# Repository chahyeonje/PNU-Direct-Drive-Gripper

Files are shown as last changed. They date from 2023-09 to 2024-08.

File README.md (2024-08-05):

# Overview

-----

# Table of Contents

- [Preparation](#preparation)
  - [Bill of Materials (BOM)](#bom)
    - [Off-the-Shelf Parts](#purchase)
    - [3D Printing](#3d-printing)
- [Actuators](#actuators)
  - [Actuator Assembly ⨉4](#assemble-actuators)
  - [Wiring](#wiring)
    - [Power Supply](#power-supply)
    - [Encoder Connection](#encoder-connection)
    - [Motor Connection](#Motor-connection)
  - [Actuator Calibration](#actuator-calibration)
    - [Calibrate ODrives](#calibrate-odrives)
    - [Calibrate Zero Position](#calibrate-zero-position)
- [Gripper](#Gripper)
  - [Finger Assembly ⨉2](#finger)
  - [Gripper Assembly](#gripper-assembly)
  - [Mounting](#mounting-ur10)
  - [Validation](#validation)
- [Customization](#customization)
  - [Mounting](#custom-mounting)
  - [Geometry](#geometry)
  - [Fingertip](#fingertip)
- [Getting Started](#getting-started)
  
-----

# Hardeware

## Bill of materials(BOM)

### Off-the-shelf parts
- [T-motor gb54-2](https://store.tmotor.com/goods-445-GB54-2.html) X 4
- [Odrive s1](https://odriverobotics.com/shop/odrive-s1) X 4
- [AS5048A Encoder + solid magnet](https://ko.aliexpress.com/item/1005004239532357.html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) X 4
- [Bearing - outer-diameter = 100mm, inner-diamter = 6mm](https://kr.misumi-ec.com/vona2/detail/221000058378/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) X 12
- [Dowel pin - diameter = 6mm, length = 10mm](https://ko.aliexpress.com/item/1005003326358562.html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) X 6
- [Wire terminal box](https://mini.freeship.co.kr/goods/content.asp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) X 1
- Shielded cable
- 3-phase cable

### 3D Printing
- [Adapter plate](stl/adapter_plate.stl/) X 4
- [Bearing spacer](stl/bearing_spacer.STL) X 12
- [Calibration arm](stl/calibration_arm.STL) X 1
- [Calibration stand](stl/calibration_stand.STL) X 1
- [Coupler](stl/coupler.STL) X 1
- [Couping](stl/coupling.stl) X 1
- [Distal link](stl/distal_link.STL) X 2
- [Distal tip link](stl/distal_tip_link.STL) X 2
- [Finger tip](stl/finger_tip.STL) X 2
- [Gripper shell](stl/gripper_shell.stl) X 1
- [Magnet holder](stl/magnet_holder.STL) X 4
- [Motor plate](stl/motor_plate.stl) X 4
- [Proximal link](stl/proximal_link.STL) X 4
<br/><br/>The gripper is designed to be compatible with Rainbow robotics RB5. For other robot systems, it should be better to design your own adapter plate and coupling.

# Actuators
## Acutator assembly
motor_with_magnet
motor-plate
actuator-module

## Wiring
The components should be connected following the diagram below. The encoder connection(black) and power connection(green) will be further elaborated.
 wiring

### Power Supply
First connect the DC power supply to the wall plug. Then connect it to the four ODrive boards, positive to positive, negetaive to negative. There is no on/off button on the boards, plug in the wall plug to turn the system on, unplug to turn it off.
power_supply

### Encoder Connection
For the encoder connection, we fabricate a cable assembly as shown below in the schematic. It is recommended to verify the connectivity and resistance of each connection to make sure the cables are soldered properly. We also recommend to label each connector like the schematic.

encoder_wiring
encoder_odrive

After successful fabrication, connect the motor encoders and the ODrives.

### Motor Connection
Keep the 3-phase connection consistent as shown below.
wiring-power
motor_odrive

### Odirve S1 Pin map.



# Actuator Calibration

Each actuator module require calibration before use. This step __can not__ be done after the gripper is assembled, so do not postpone this step.

We explicitly define the `direction of the rotor` to be the direction the hexagonal logo on the rotor is pointing at, and the `zero position of the motor` to be when the direction of the motor is pointing at the opposite direction of the power port on the stator. 

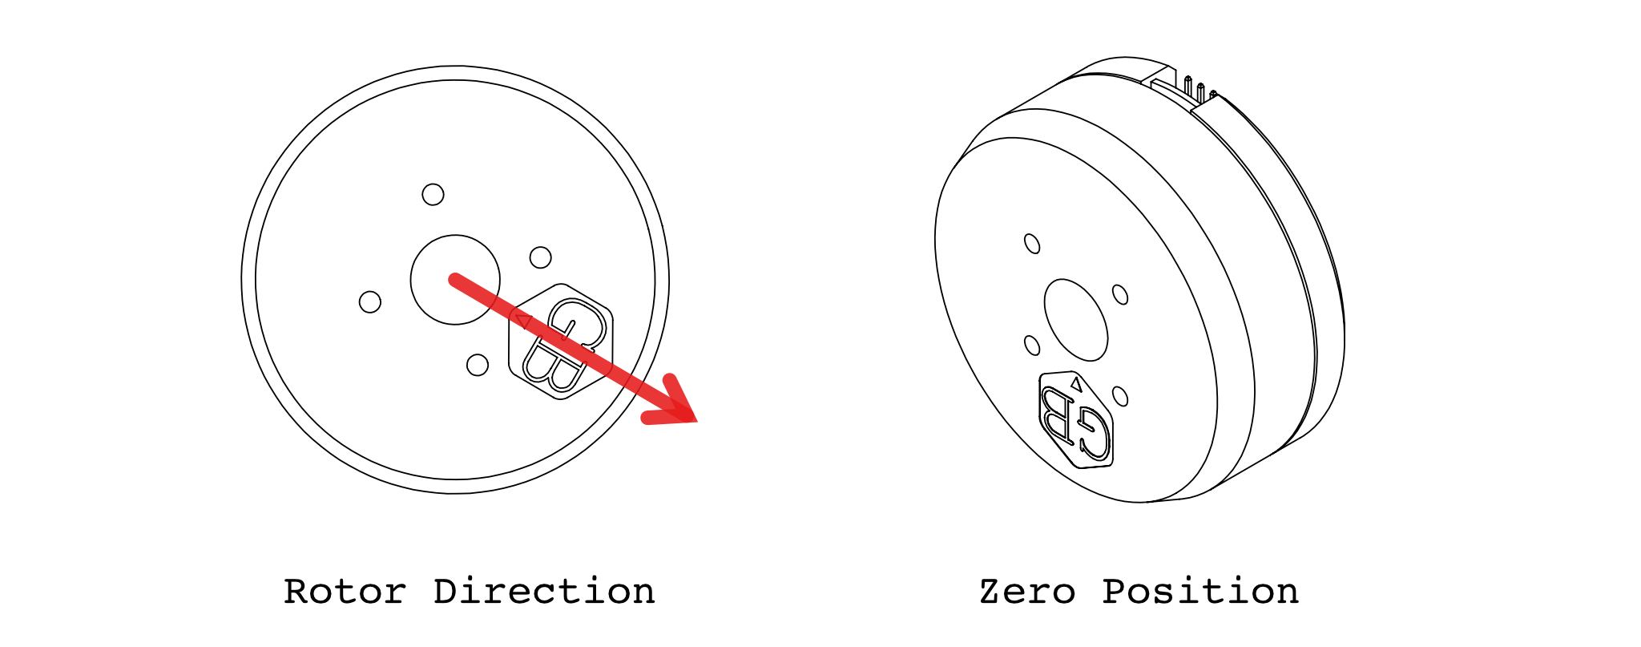
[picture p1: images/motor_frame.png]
motor-zero


## Calibrate ODrives

## Calibrate Zero Position

Here we calibrate the zero position of the motor. Mount the actuator on the calibration stand and install the calibration arm onto the actuator according to the diagram

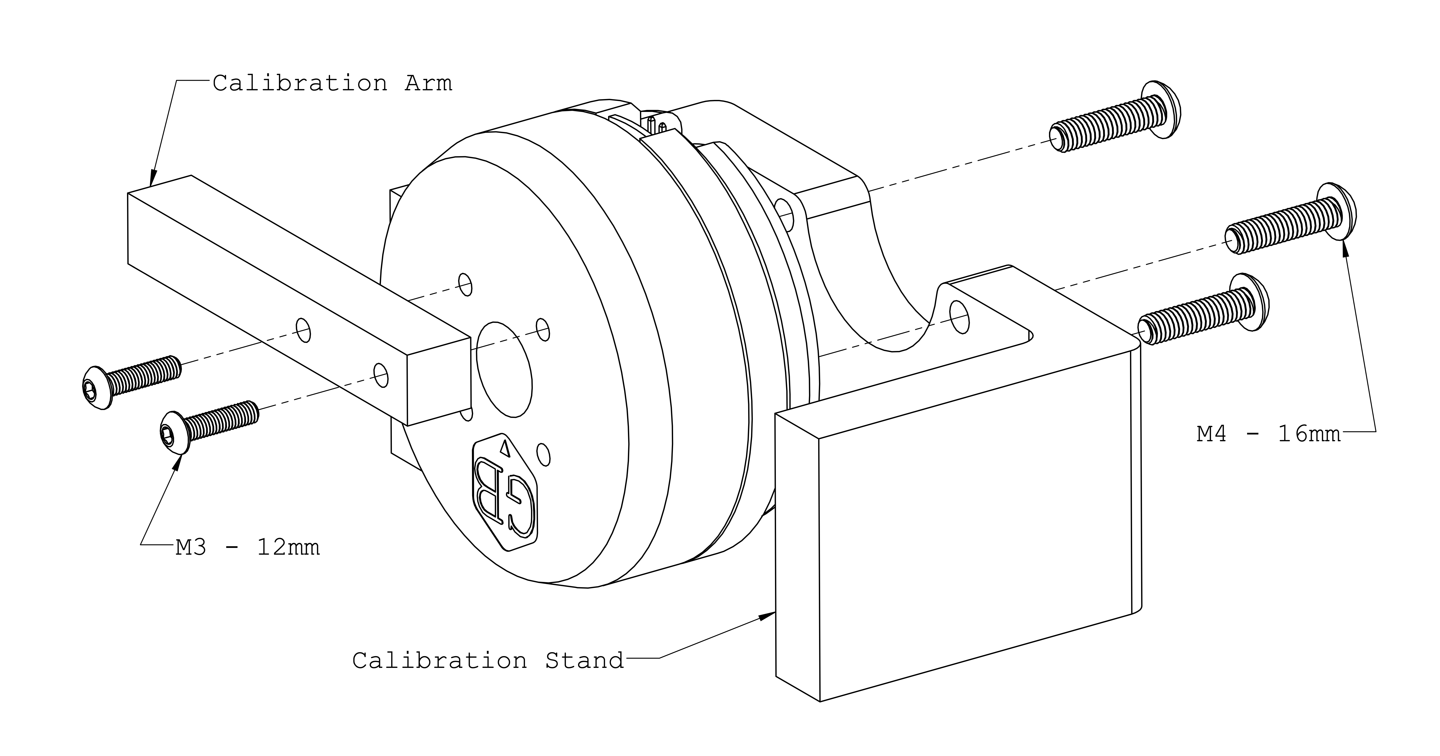
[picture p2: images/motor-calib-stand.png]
calibration-stand


Put the motor into zero position as show in the diagram below. Press down the calibration arm to make sure the stand and arm touch tightly. 

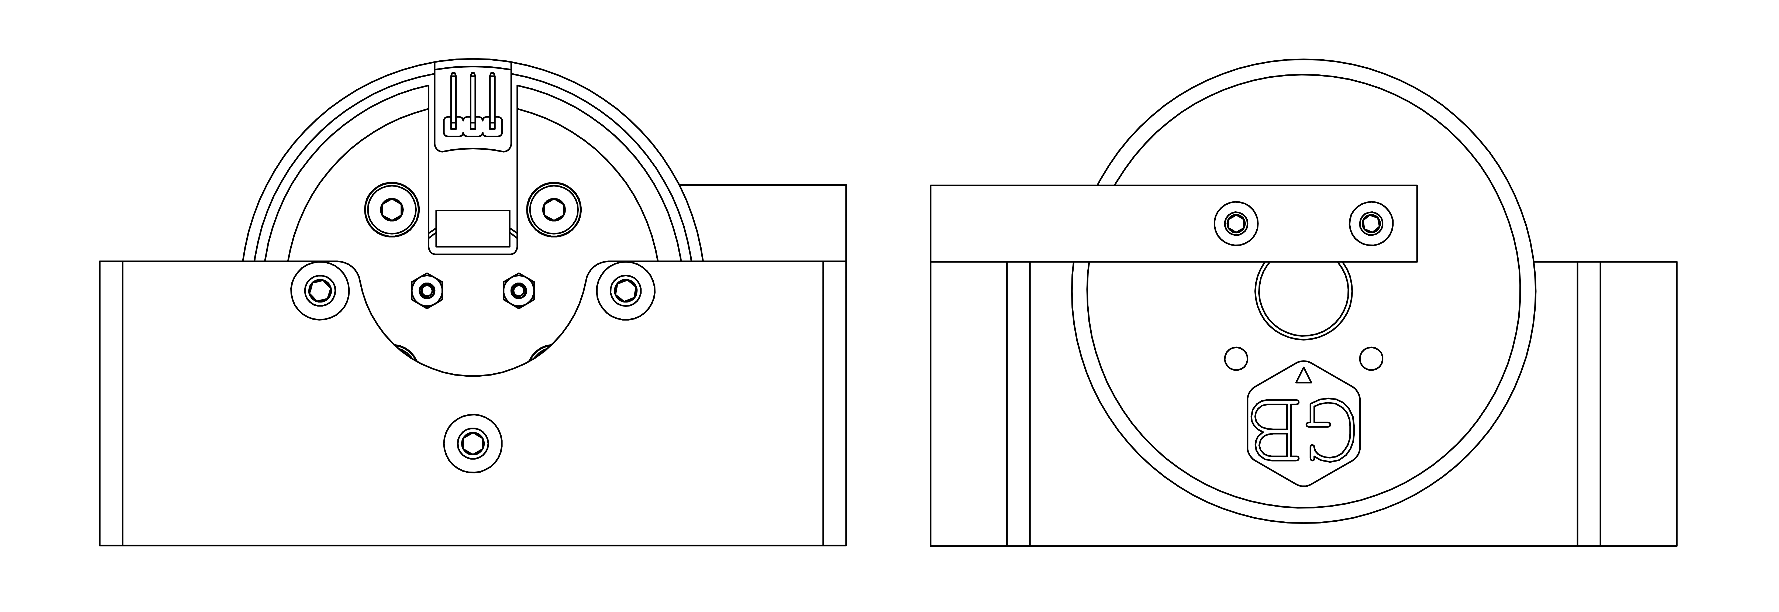
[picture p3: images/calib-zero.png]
zero-stop


It should be zero when motor is in [zero position](#zero-position-of-the-motor). Also try 90° and 180°. Don't mind the sign at this stage of assembly.

# Gripper

## Finger Assembly ⨉ 2

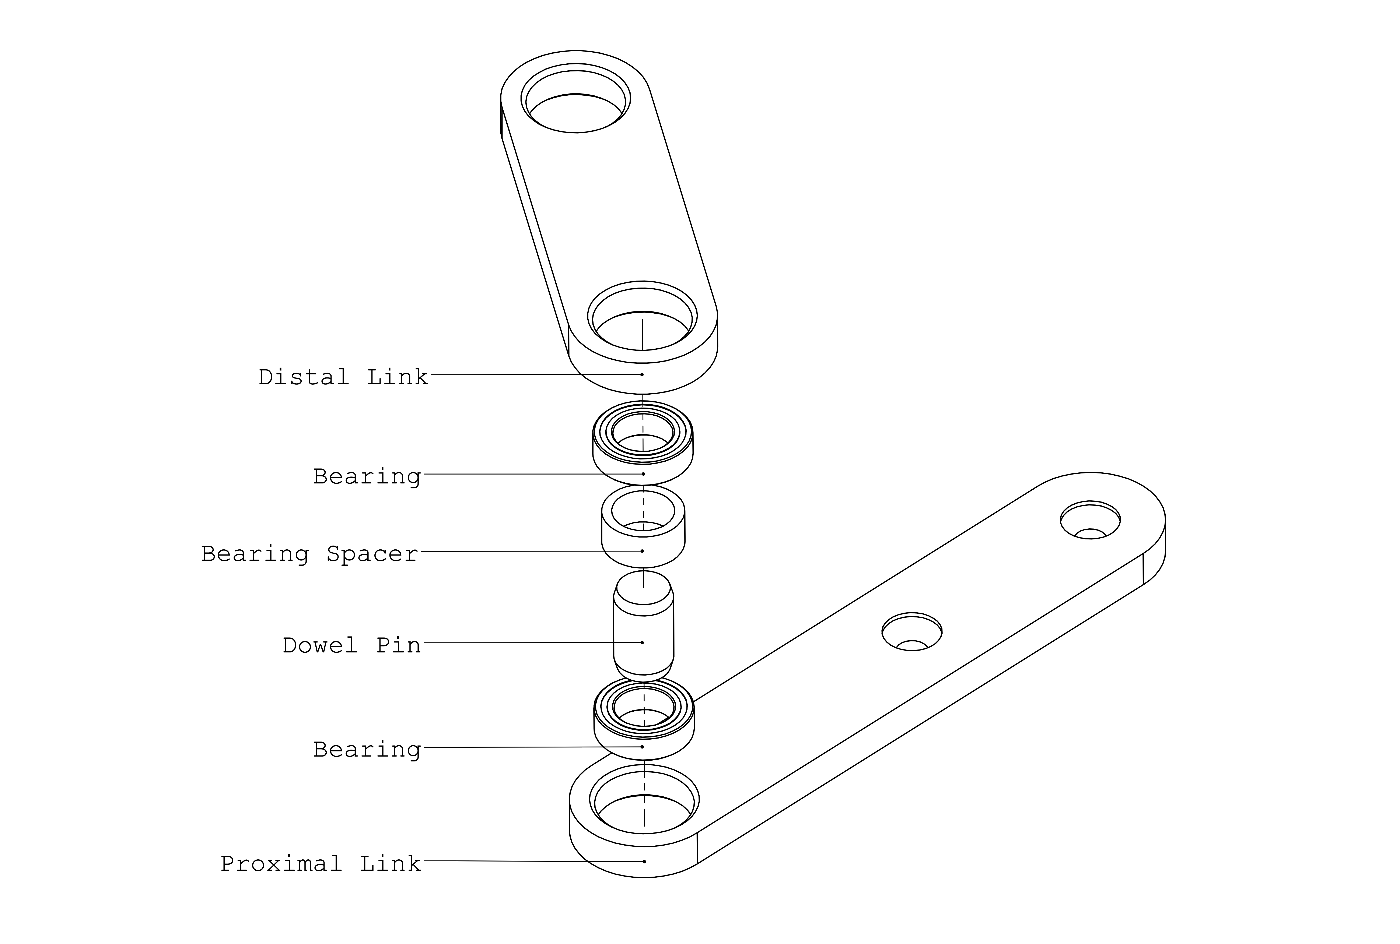
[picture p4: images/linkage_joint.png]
linkage_joint


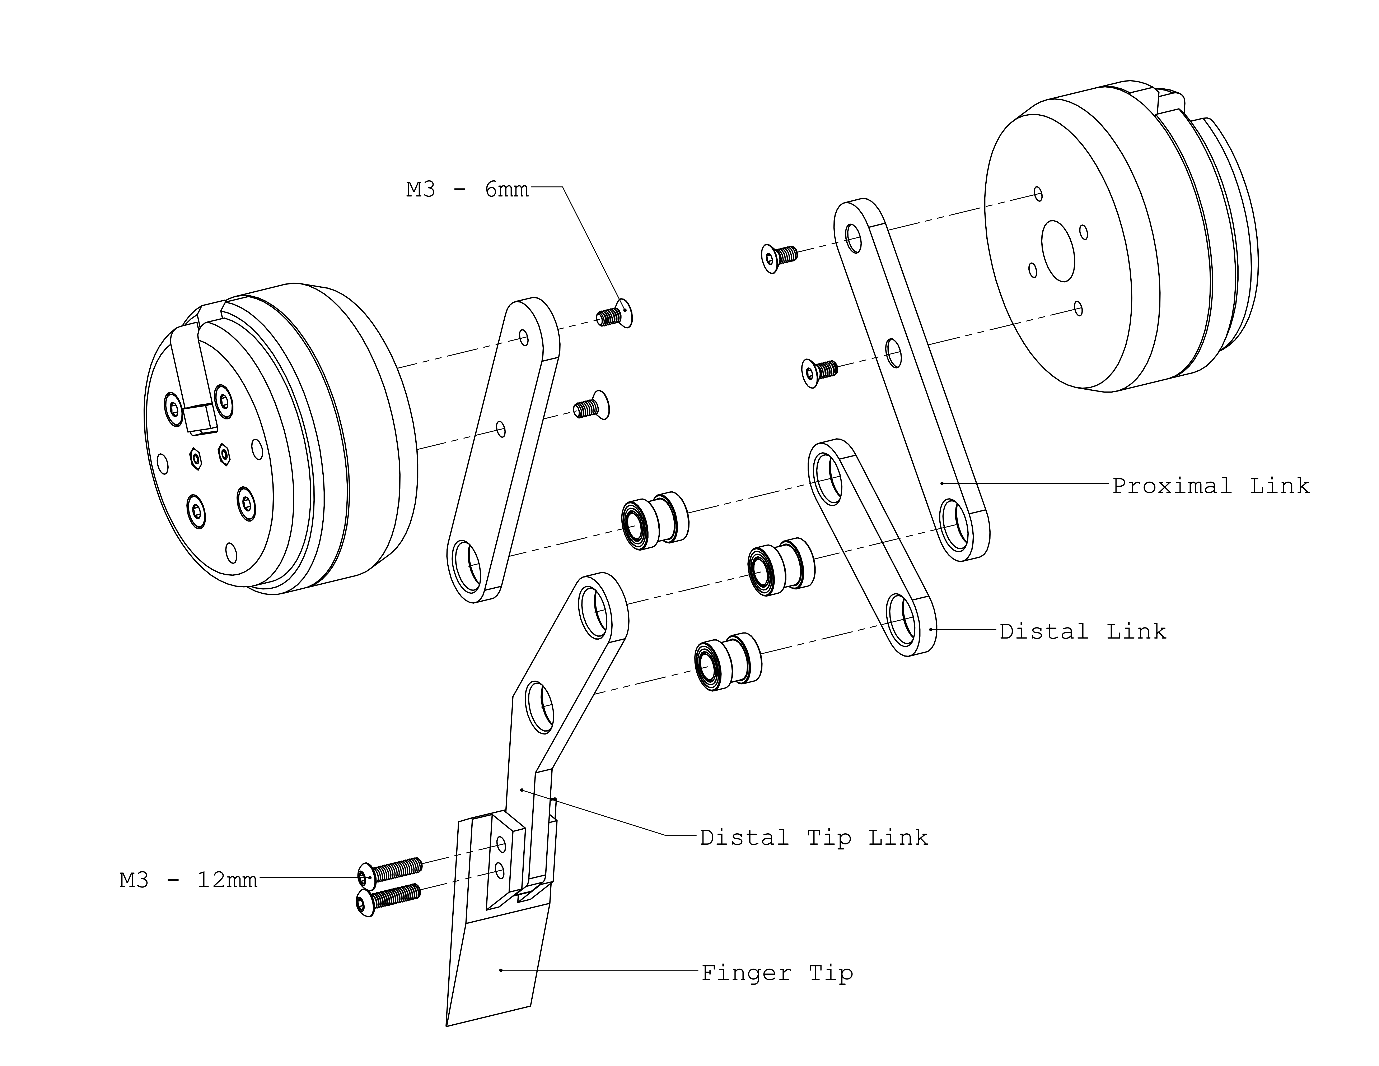
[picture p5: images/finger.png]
finger


## Gripper Assembly

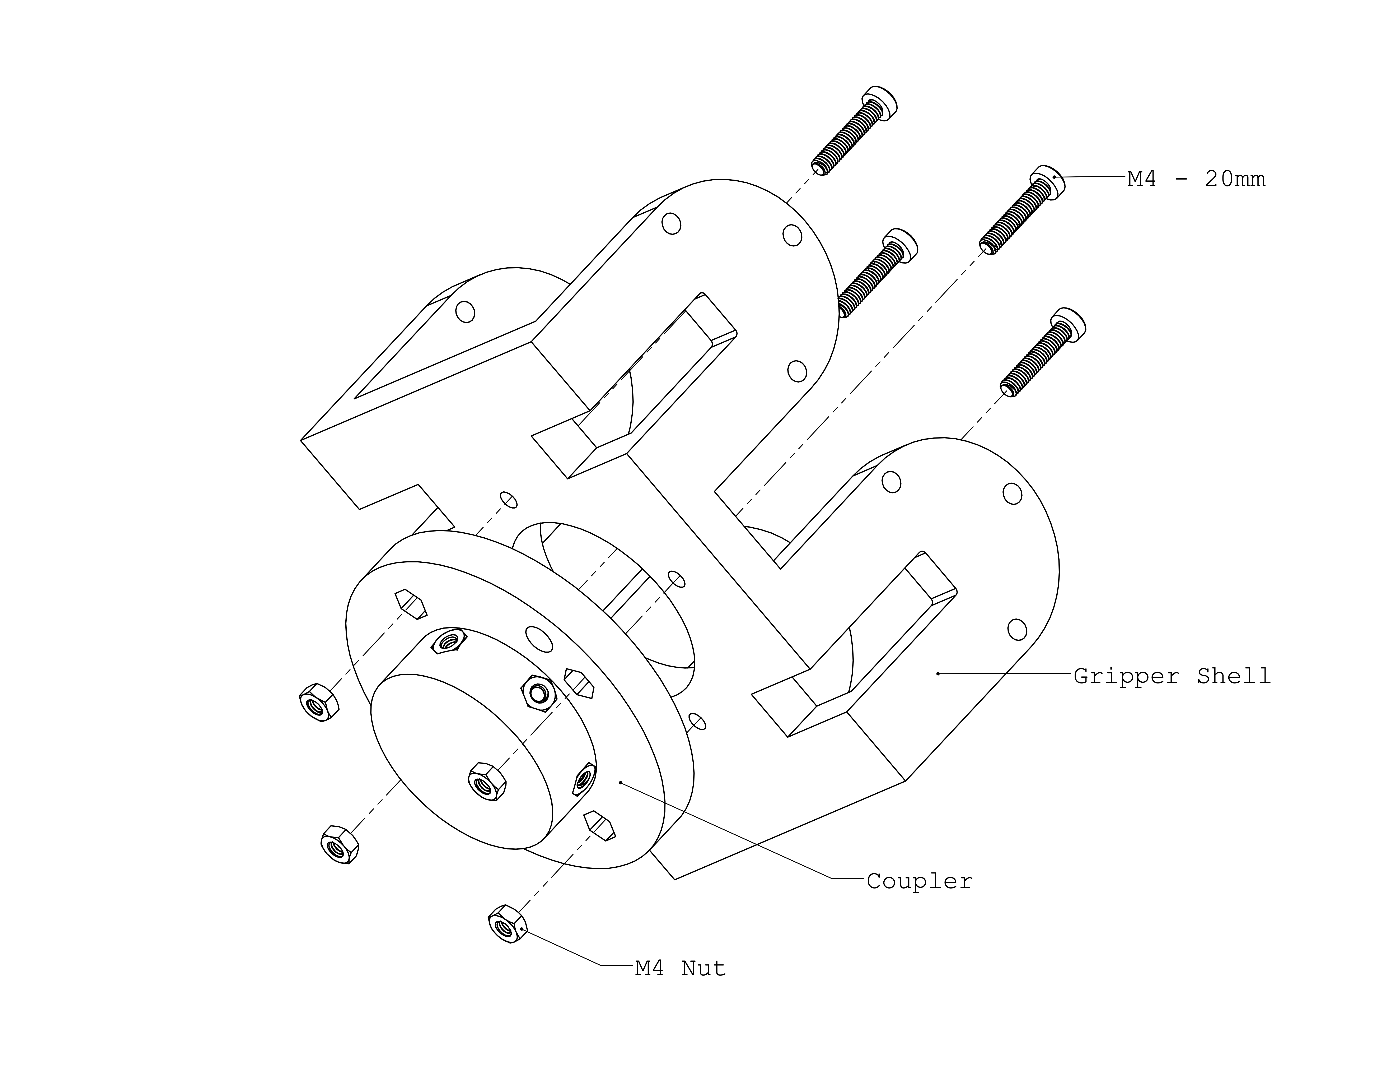
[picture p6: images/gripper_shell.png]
gripper_shell


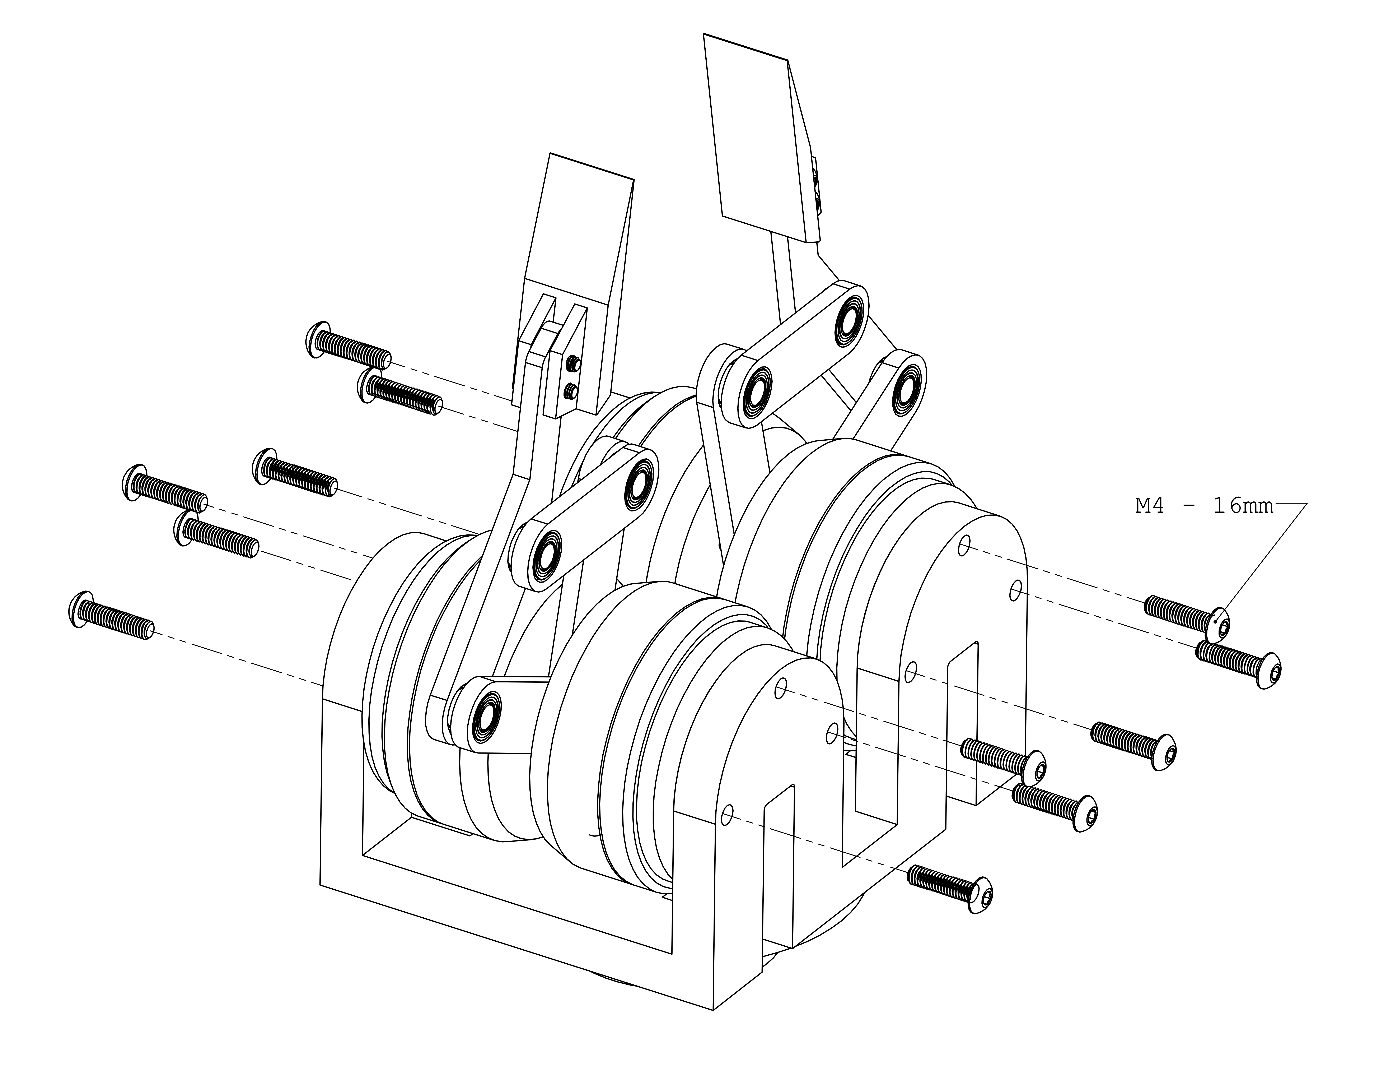
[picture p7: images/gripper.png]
gripper


## Mounting

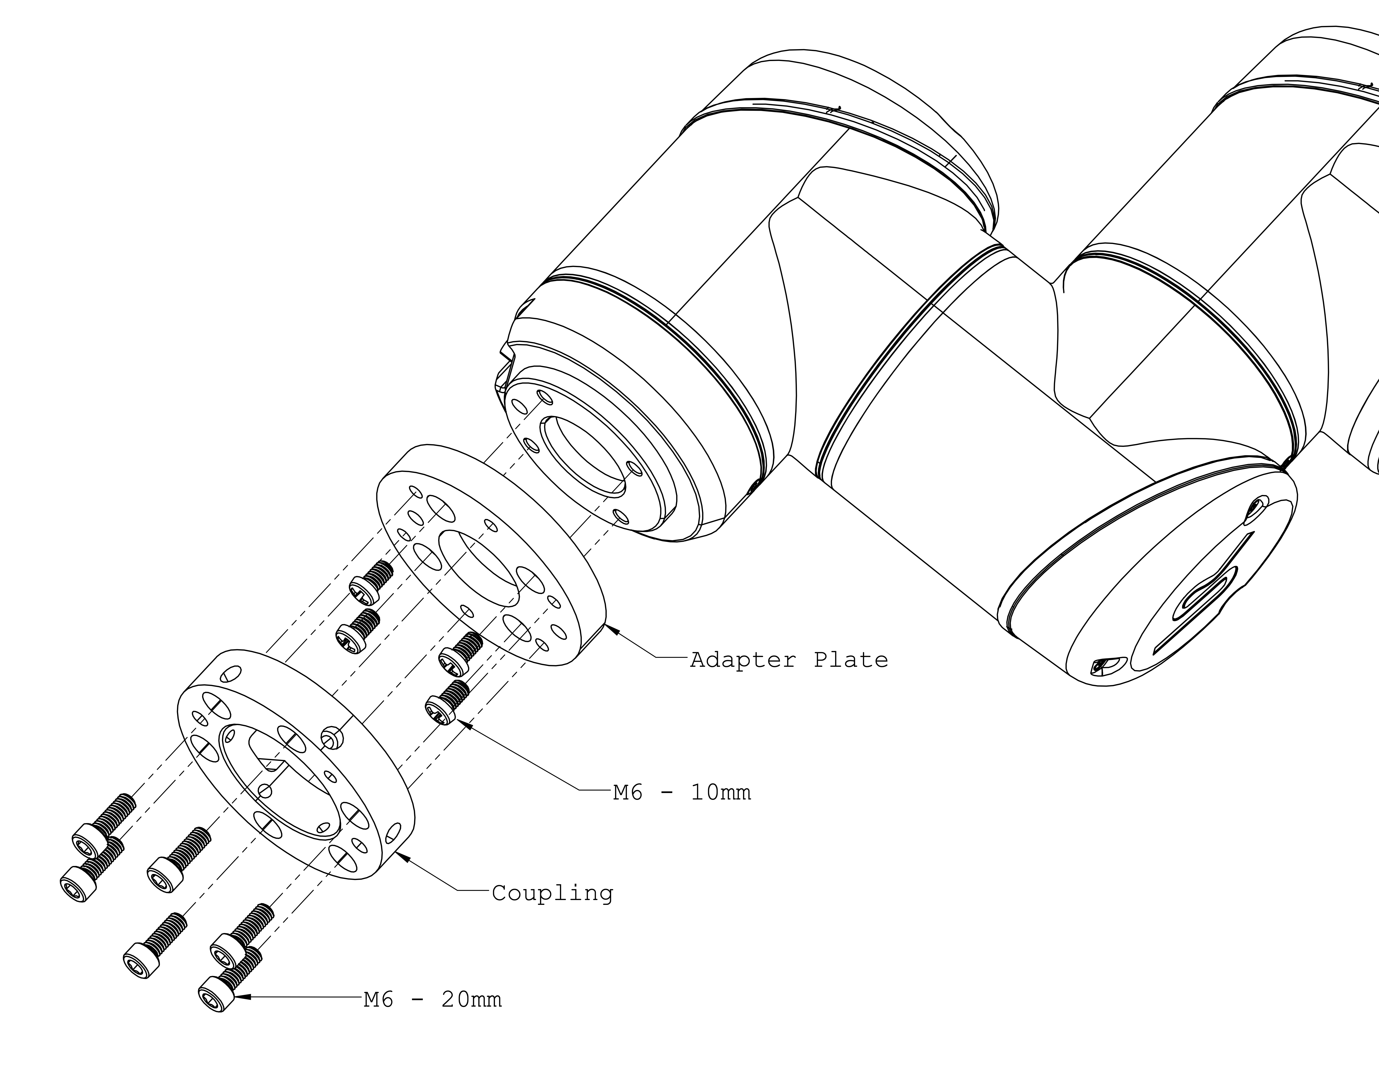
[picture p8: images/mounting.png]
mounting


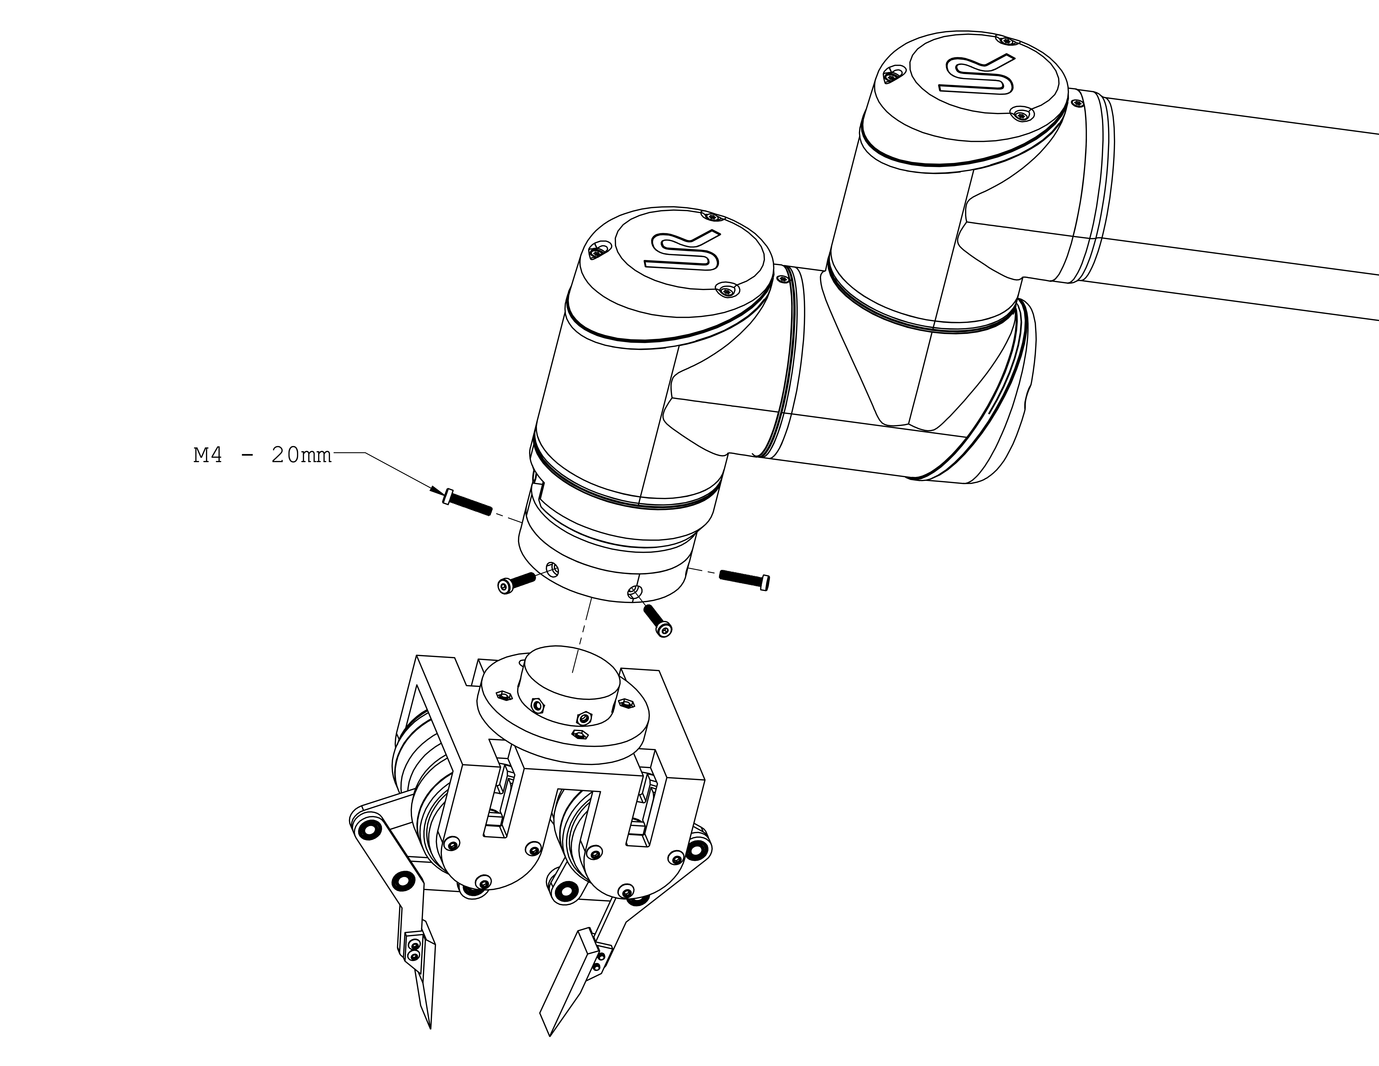
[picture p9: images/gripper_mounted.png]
gripper_mounted


## Validation

# Customization

## Mounting

If the default mounting does not work for you, it's very easy to make a custom mount. The gripper has a __60 mm PCD with 4 ⨉ M4__ mounting interface, as shown in the drawing below.

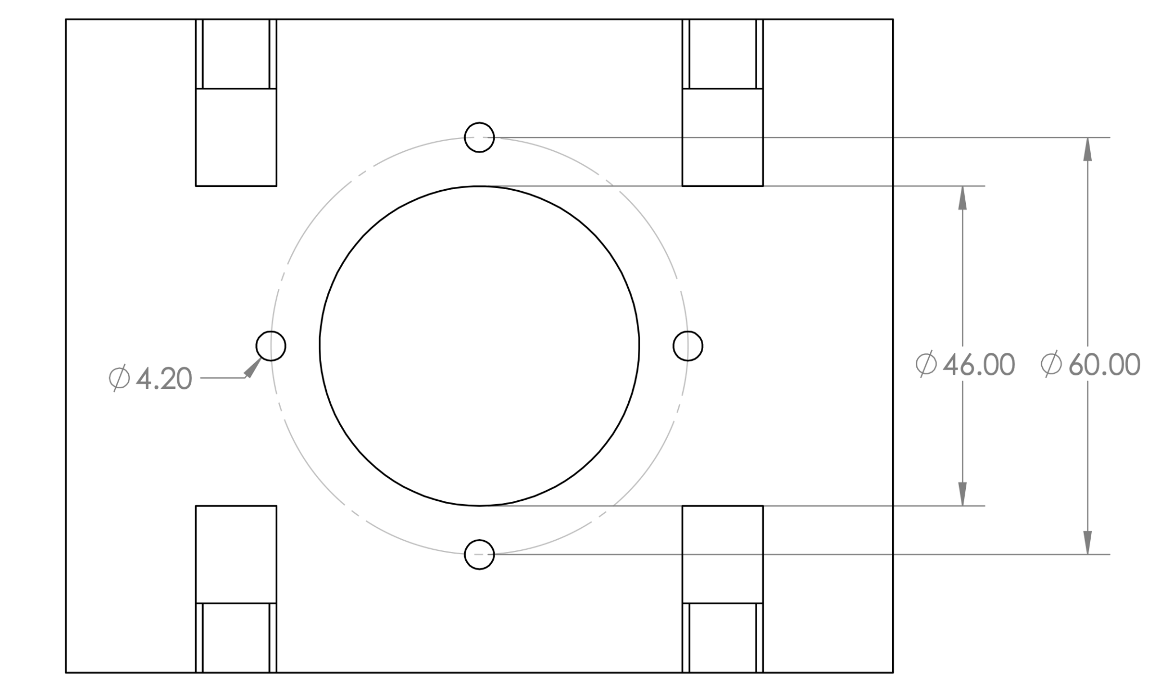
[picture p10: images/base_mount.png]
base_mount


## Geometry

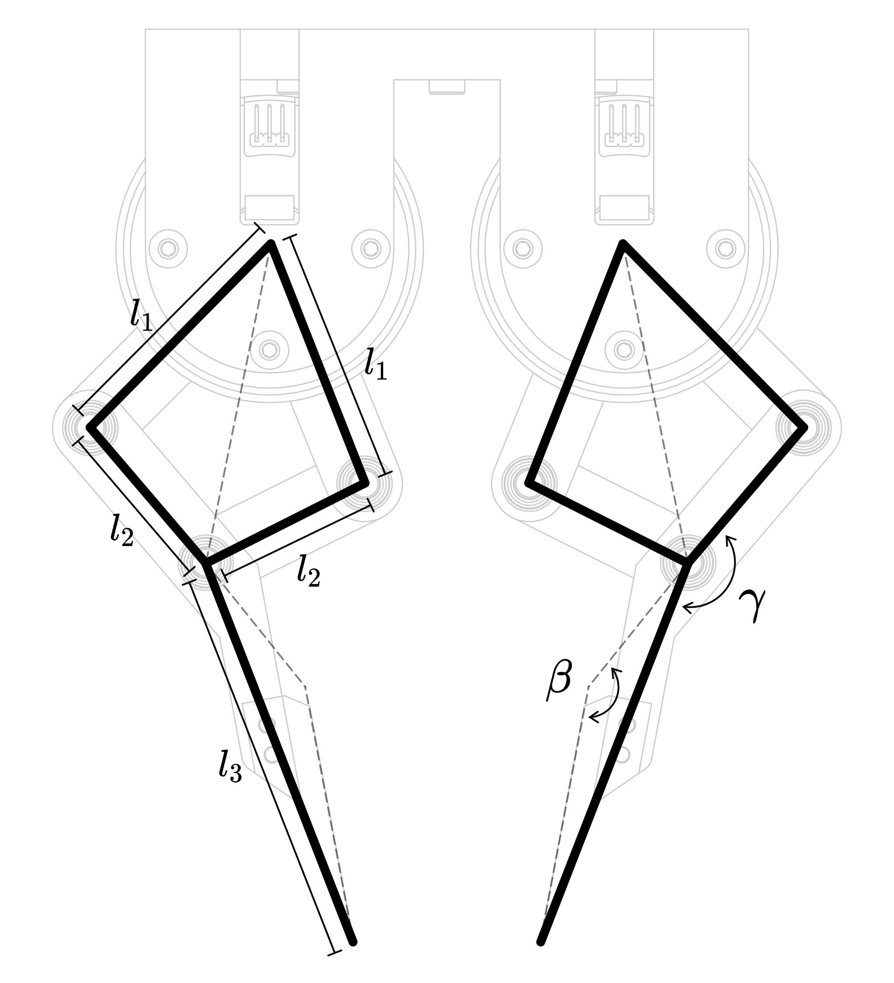
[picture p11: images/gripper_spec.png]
geometry


The geometrical parameters can be customized. After you design your custom parts, update the `ddh_driver/config/default.yaml` so the driver can work properly. 

| Parameter | Configuration Path | Unit |
|----|---|-----|
| ℓ₁ | `/geometry/l1` | mm |
| ℓ₂ | `/geometry/l2` | mm |
| ℓ₃ | `/geometry/l3` | mm |
| 𝝱 | `/geometry/beta` | degree |
| 𝛄 | `/geometry/gamma` | degree |

## Fingertip

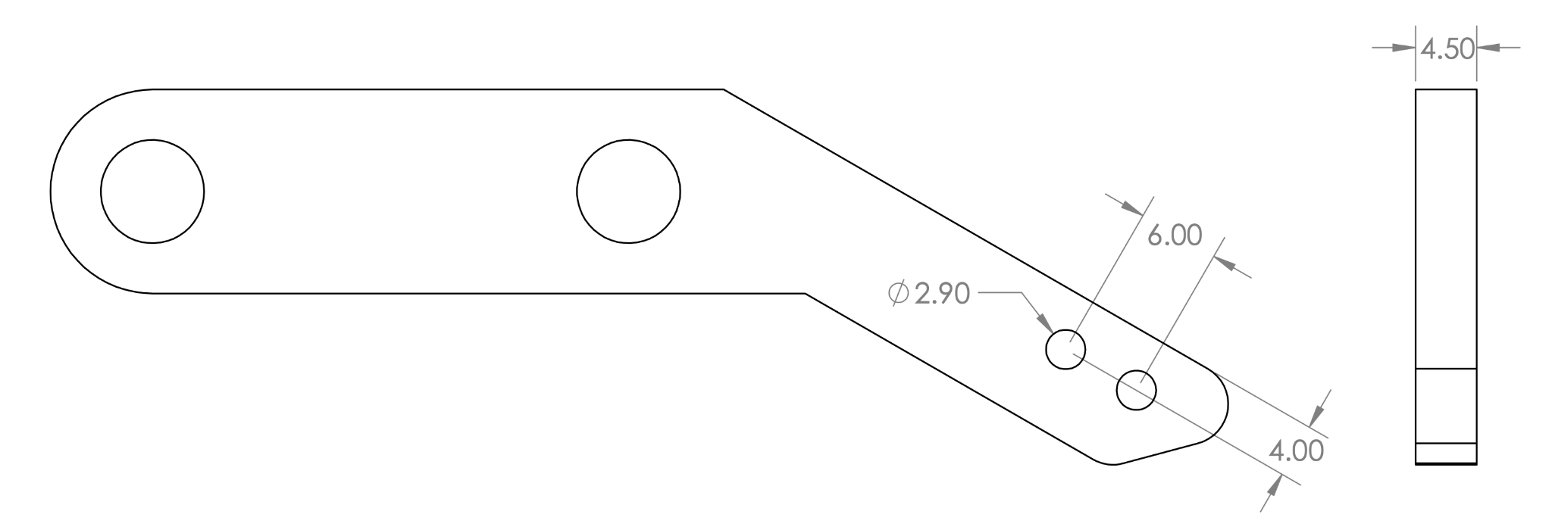
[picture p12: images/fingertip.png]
fingertip


-----
# Software
Our software is implemented with **python3** and tested on **Ubuntu**. You can also refer to this website https://docs.odriverobotics.com/v/latest/guides/getting-started.html.

### Versions ###
- ubuntu : 20.04
- Python : 3.10.11
- Odrive control untility : 0.6.7

### Getting started ###
1. First, you should install accompanying PC program for the ODrive, 'odrivetool'.
```bash
pip install --upgrade odrive
```
2. Set up USB device permissions.
```bash
sudo bash -c "curl https://cdn.odriverobotics.com/files/odrive-udev-rules.rules > /etc/udev/rules.d/91-odrive.rules && udevadm control --reload-rules && udevadm trigger"
```
3. To launch the main interactive ODrive tool, type 'odrivetool'. And then, type 'odrv0.vbus_voltage' to inspect the boards main supply voltage.
```bash
odrivetool
```
&nbsp;&nbsp;&nbsp;&nbsp;If the program is installed and the odrive is connected successfully, then you can see the messages.
```bash
ODrive control utility v0.6.7
Please connect your ODrive
You can also type help() or quit().

Connected to ODrive S1 384D34783539 (firmware v0.6.7) as odrv0
In  [1]: odrv0.vbus_voltage
Out [1]: 23.931137084960938
```
-----

# Contributors
- Hyeonje Cha, guswp3611@gmail.com
- Seunghwa Oh, seunghwa9118@pusan.ac.kr

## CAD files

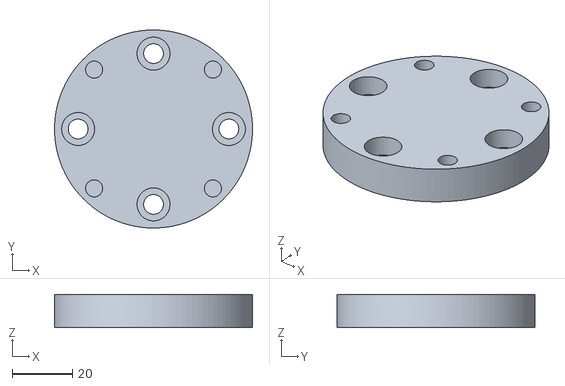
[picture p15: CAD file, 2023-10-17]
stl/adapter_plate.stl
66.0 x 66.0 x 11.0

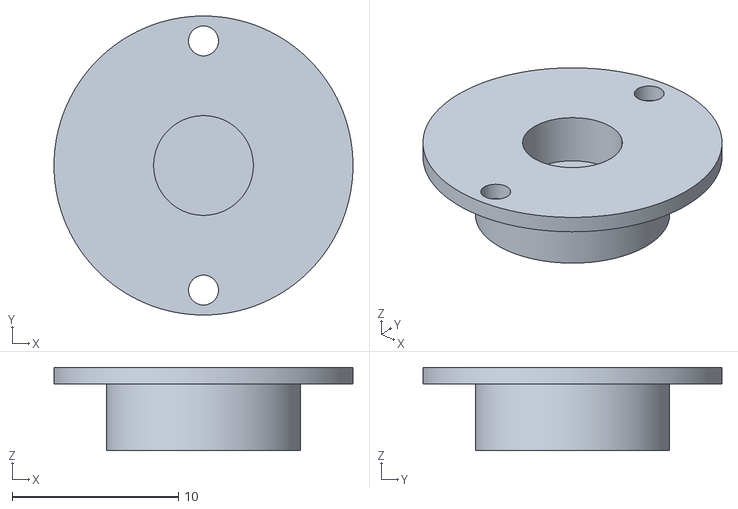
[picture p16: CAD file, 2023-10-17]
stl/magnet_holder.STL
18.0 x 18.0 x 5.00

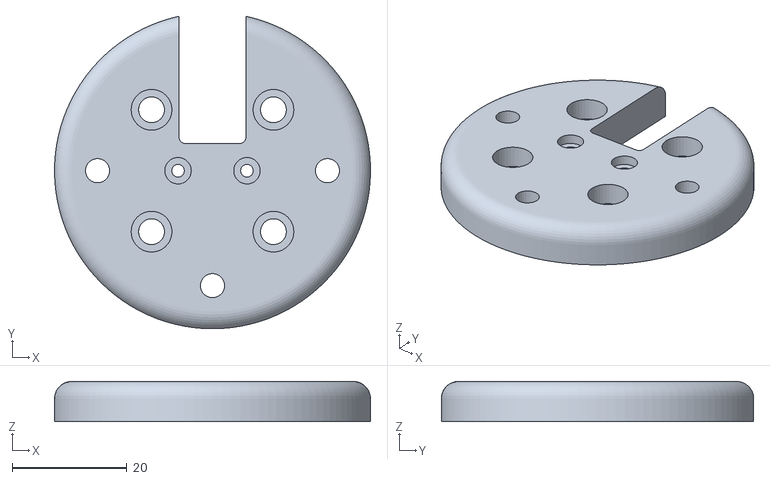
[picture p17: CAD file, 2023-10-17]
stl/motor_plate.stl
55.0 x 54.4 x 7.00

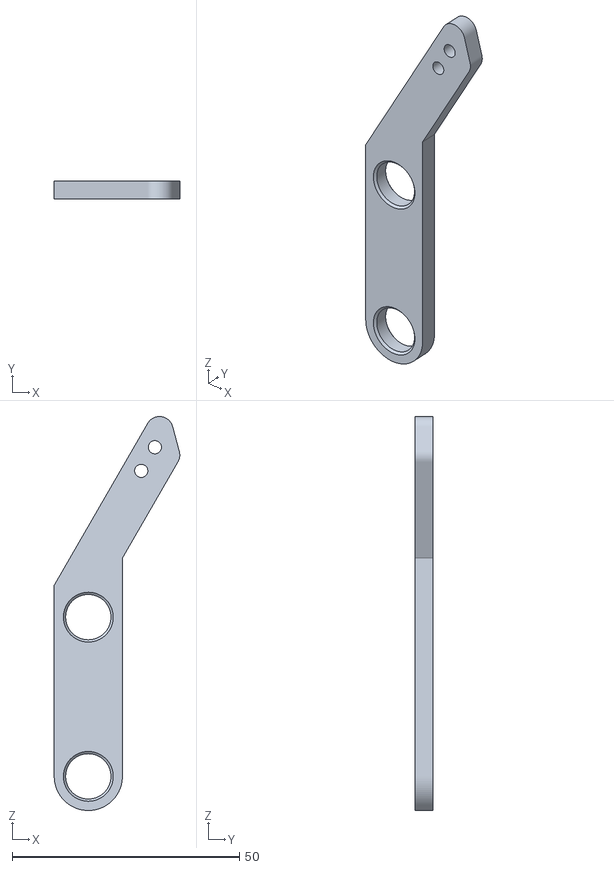
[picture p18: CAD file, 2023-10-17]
stl/distal_tip_link.STL
27.6 x 4.00 x 86.6

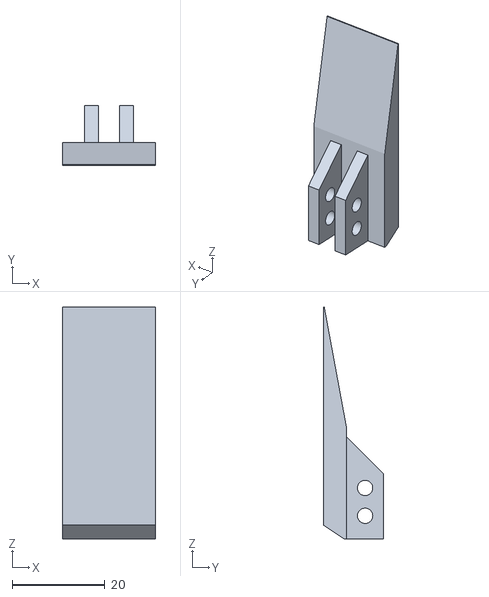
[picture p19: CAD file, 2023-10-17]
stl/finger_tip.STL
20.0 x 13.0 x 50.0

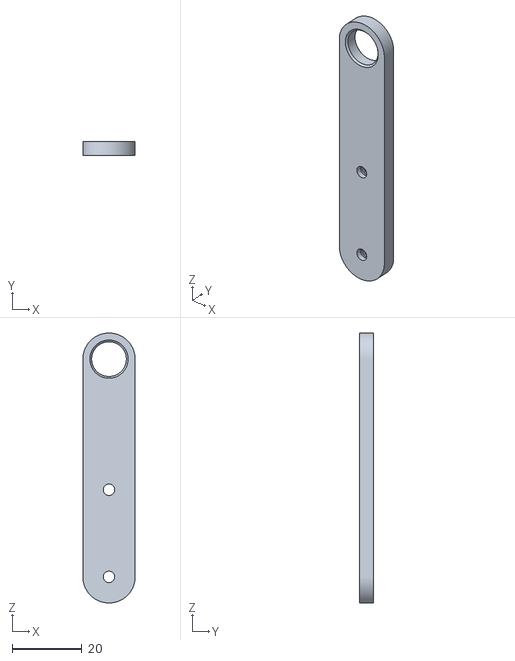
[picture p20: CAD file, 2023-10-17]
stl/proximal_link.STL
15.0 x 4.00 x 77.5

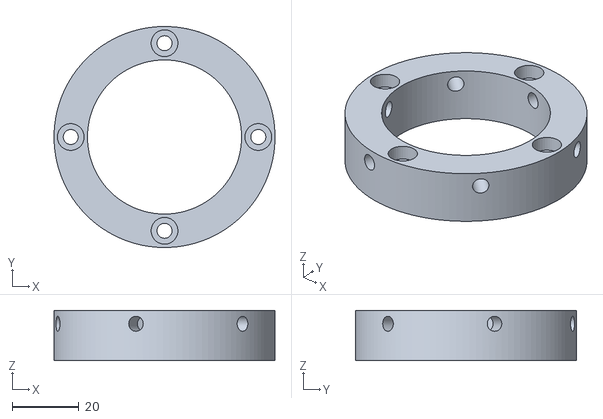
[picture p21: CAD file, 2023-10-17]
stl/coupling.stl
66.0 x 66.0 x 15.0

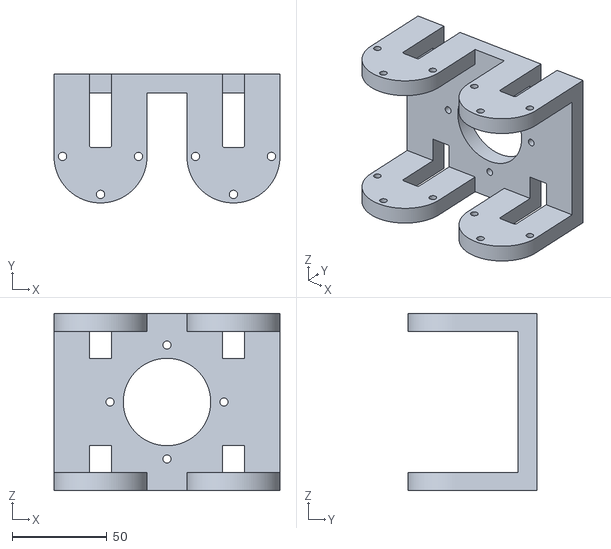
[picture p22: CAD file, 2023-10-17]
stl/gripper_shell.stl
119.0 x 67.8 x 93.4

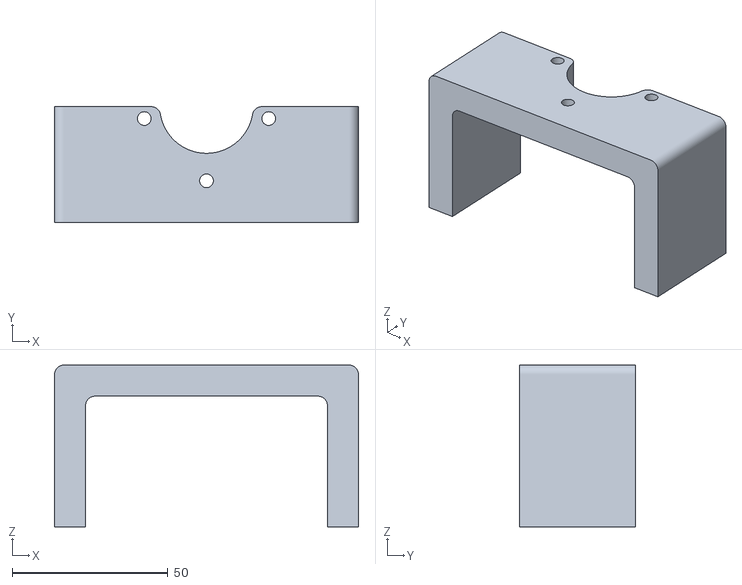
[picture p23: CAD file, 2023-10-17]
stl/calibration_stand.STL
97.7 x 37.2 x 52.0

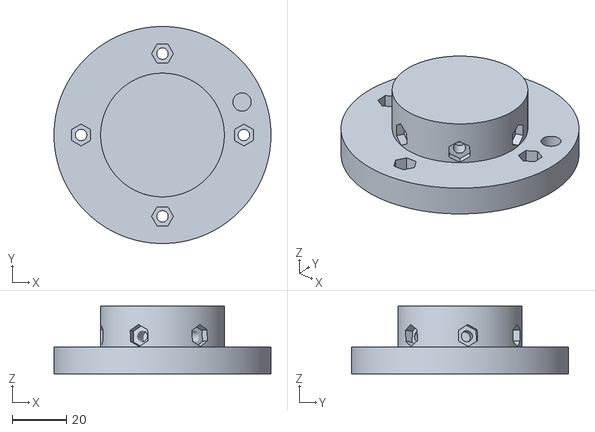
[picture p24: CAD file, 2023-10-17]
stl/coupler.STL
80.0 x 80.0 x 25.0

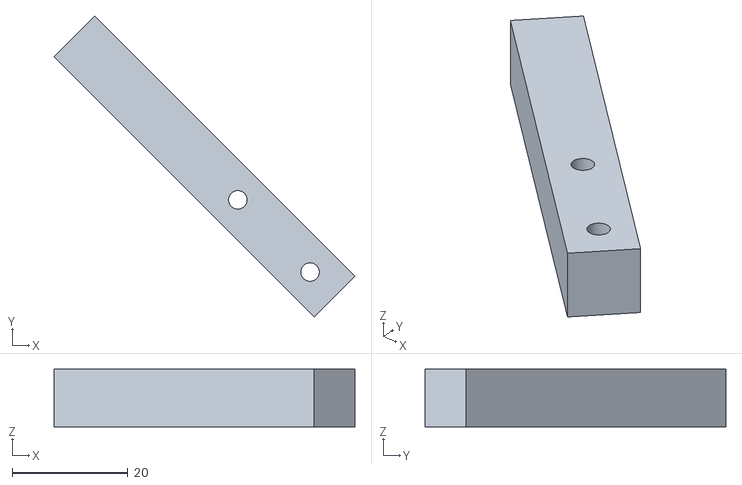
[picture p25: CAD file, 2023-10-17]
stl/calibration_arm.STL
52.1 x 52.1 x 10.0

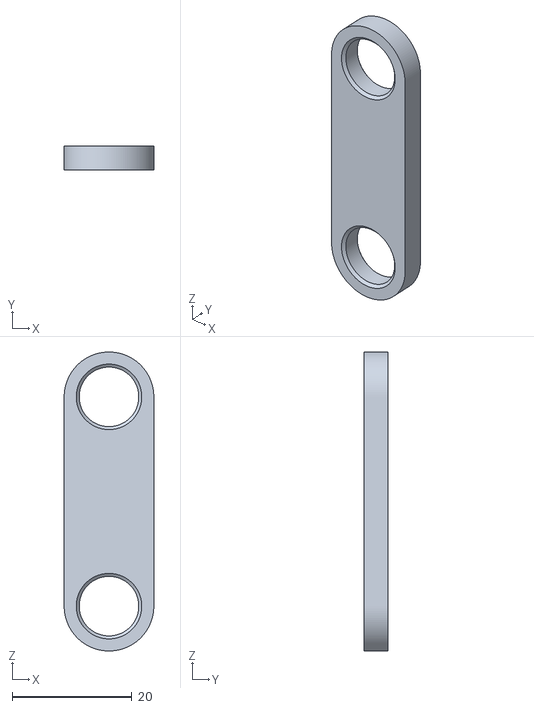
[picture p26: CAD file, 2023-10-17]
stl/distal_link.STL
15.0 x 4.00 x 50.0

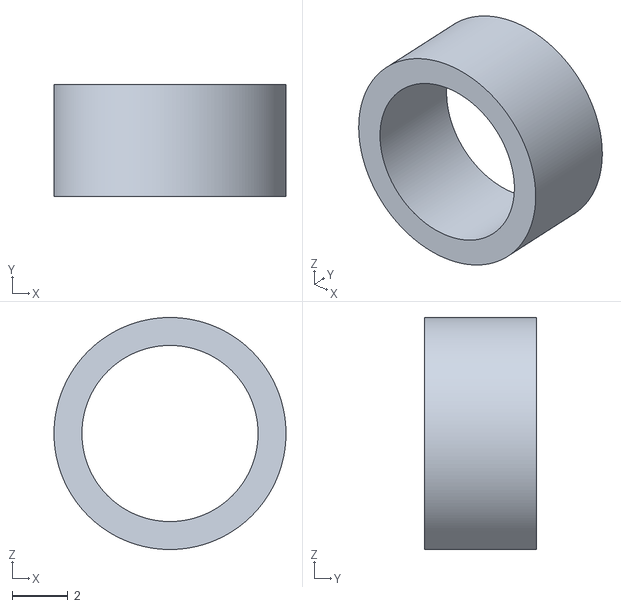
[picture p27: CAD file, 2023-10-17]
stl/bearing_spacer.STL
8.30 x 4.00 x 8.30

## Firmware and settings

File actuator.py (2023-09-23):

from odrive.enums import *

class Actuator(object):

    def __init__(self, odrv, encoder_offset, direction, link_offset):
        self.odrv = odrv
        self.axis = odrv.axis0
        self.encoder_offset = encoder_offset
        self.direction = direction
        self.link_offset = link_offset

    @property
    def encoder(self):
        return self.odrv.encoder_estimator1.pos_estimate

    @property
    def motor_pos(self):
        return 360 * self.direction * (self.odrv.encoder_estimator1.pos_estimate - self.encoder_offset)

    @motor_pos.setter
    def motor_pos(self, setpoint):
        self.axis.controller.input_pos = (setpoint / 360.) * self.direction + self.encoder_offset

    @property
    def theta(self):
        return self.motor_pos + self.link_offset

    @theta.setter
    def theta(self, setpoint):
        self.motor_pos = setpoint - self.link_offset

    @property
    def armed(self):
        return self.axis.current_state is AXIS_STATE_CLOSED_LOOP_CONTROL

    @armed.setter
    def armed(self, val):
        if val:  # arm
            self.axis.controller.config.input_mode = INPUT_MODE_POS_FILTER  # INPUT_MODE_PASSTHROUGH
            self.axis.requested_state = AXIS_STATE_CLOSED_LOOP_CONTROL
        else:  # disarm
            self.axis.requested_state = AXIS_STATE_IDLE

    @property
    def stiffness(self):
        return self.axis.controller.config.pos_gain

    @stiffness.setter
    def stiffness(self, val):
        self.axis.controller.config.pos_gain = val

    @property
    def vel_gain(self):
        return self.axis.controller.config.vel_gain

    @vel_gain.setter
    def vel_gain(self, val):
        self.axis.controller.config.vel_gain = val

    @property
    def bandwidth(self):
        return self.axis.controller.config.input_filter_bandwidth

    @bandwidth.setter
    def bandwidth(self, val):
        self.axis.controller.config.input_filter_bandwidth = val

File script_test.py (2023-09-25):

import odrive
from odrive.enums import *
from actuator import *

SN_L0 = '384D34783539'
SN_L1 = '383F34723539'

odrv0 = odrive.find_any(serial_number=SN_L0)
odrv1 = odrive.find_any(serial_number=SN_L1)

leftFinger0 = Actuator(odrv0, 0.96, 1, 45)
leftFinger1 = Actuator(odrv1, 0.97, 1, 45)

print(str(leftFinger0.encoder))
print(str(leftFinger1.encoder))
print(str(leftFinger0.motor_pos))

odrv0.clear_errors()
odrv1.clear_errors()

odrv0.axis0.requested_state = AXIS_STATE_FULL_CALIBRATION_SEQUENCE
odrv1.axis0.requested_state = AXIS_STATE_FULL_CALIBRATION_SEQUENCE
# print(str(odrv0))
# print(str(odrv1))

# print(str(odrv0.encoder_estimator1.pos_estimate))
# print(str(odrv1.encoder_estimator1.pos_estimate))

# while(True)
# odrv0.axis0.requested_state = AXIS_STATE_CLOSED_LOOP_CONTROL
# odrv1.axis0.requested_state = AXIS_STATE_CLOSED_LOOP_CONTROL

# 1. Attack point 1
# odrv0.axis0.controller.input_pos = 0.80
# odrv1.axis0.controller.input_pos = 1.09
# odrv0.axis0.controller.input_pos = 1.06
# odrv1.axis0.controller.input_pos = 0.99

# 2. Attack point 2
# odrv0.axis0.controller.input_pos = 0.80
# odrv1.axis0.controller.input_pos = 1.12
# odrv0.axis0.controller.input_pos = 0.93
# odrv1.axis0.controller.input_pos = 1.10

# 3. Attack point 3
# odrv0.axis0.controller.input_pos = 0.93
# odrv1.axis0.controller.input_pos = 1.03
# odrv0.axis0.controller.input_pos = 1.03
# odrv1.axis0.controller.input_pos = 1.0

# odrv0.axis0.requested_state = AXIS_STATE_IDLE
# odrv1.axis0.requested_state = AXIS_STATE_IDLE

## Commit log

2023-09-25 Added calibration state
2023-10-17 Added stl files.
    [adapter plate.stl, bearing spacer.STL, calibration_arm.STL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]
2023-10-17 Added stl files(updated version)
    [adapter_plate.stl, bearing_spacer.STL, calibration_arm.STL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]
